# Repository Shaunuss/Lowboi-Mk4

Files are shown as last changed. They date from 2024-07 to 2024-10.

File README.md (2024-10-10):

# **Lowboi Mk4 15:1**

## Badass lightweight worm drive extruder.

Lowboi Mk4 - 003

## PARTS DESCRIPTION  
The drivetrain on Lowboi Mk4 uses a single piece gear hob and bearing idler configuration, resulting in a very smooth and high extrusion quality, practically eliminating the common woodgrain artifacting seen in numerous other extruders. This is down to the gear hob being one piece and fully concentric, and no gear meshing issues sometimes seen in dual drive gear extruders. *Bill of materials is at the bottom.*

*NOTE:* The body/housing of Lowboi Mk4 has been updated with internal reinforcing to strengthen the housing against cracking along layer lines. Following print, you need to superglue two 20mm long pieces of filament up inside two holes from underneath. See video in build tips for more details.

*Optional printed toolboard motor mount bracket is available in the files list.* (requires M3 x 30 capscrews for mounting through motor)

## GEAR  
**K1 steel drive gear hob with DLC coating** is sourced from **AliExpress**, originally intended as an upgrade part for the Creality K1 extruder. I used gears from Mellow and am very happy with the quality. Gear and bearing quality may vary depending on vendor, so I recommend the use of high quality **NSK bearings** including replacing the stock bearing that comes with the gear.


## WORM  
Worm is a high quality steel worm from **KHK** which can come in one or two start configuration, ***cut down to 12mm long***. You are looking at the two start version of the Lowboi Mk4 with a **15:1 drive ratio**. I have also made an extruder body for the one start version for 30:1 drive ratio.


## GREASE  
It is recommended to use grease containing **molybdenum disulphide** for lubricating the worm and gear, for it's increased anti wear properties.


## IDLER BEARING  
Idler is a small bearing mounted in the latch on a **GCR15 bearing steel shaft**. It is technically a fixed unfixed idler without spring, with only a tiny amount of flex in the tensioning latch itself. This provides very strong grip on the filament by the hob.


## MOTOR  
Lowboi Mk4 uses a **NEMA14 36mm** pancake motor with 5mm D shaft configuration.

The **LDO-36STH20-1004AH-RevA-1** motor has 0.1Nm of torque, and can be sourced from Mellow on Aliexpress as a replacement motor for their Cannon extruder. This motor will work, but it becomes a bottleneck and will skip before you run out of grip on the hob.

For a significant torque increase, the BOM specifies a MOONs **CSE14HRA2L4100** motor which has 0.19Nm of torque for considerably more extrusion force, and can be sourced from Formbot's website. You will never run out of torque with this motor.
Motors

## FLOW TESTS
I carry out open air extrusions tests to see flow capability. I tend to use grey or black ASA at 260°C because this filament is a mainstay of my prints. The following tests were all conducted using the same spool of filament, at 260°, unless stated otherwise. 

With the LDO motor, Lowboi Mk4 has been tested to flow up to **31mm^3/s** through a Trianglelab Dragon Ace hotend with the stock 0.4mm nozzle.

With the MOONs motor, the Dragon Ace hotend was able to flow **~35mm^3/s** max on the stock 0.4mm nozzle.

With the addition of the CHT Melt Zone Extender, max flow increased to **45.7mm^3/s**.

Swapping to a 0.5 Bozzle Nozzle increased max flow to **60.1mm^3/s**.

Increasing hotend temp to 300°C increase max flow to **70mm^3/s**.

# 60.1mm^3/s run
https://github.com/user-attachments/assets/7bbf58c4-ef9b-4407-a020-078142051459

# Slow-motion printing vid showing worm drive in action.
https://github.com/user-attachments/assets/c63346ed-cf1d-420c-8268-6457a2b93abd

## BUILD TIPS  
I have printed this in **Polycarbonate**, and **ASA**. Both have worked well.

Print orientation is standing in the normal upright position, on the foot flange, 0.2 layer height with 100% infill, and using automatic supports.

After printing and removing supports, run a 2mm drill bit down through the filament tunnel all the way through the extruder to clear any burrs and prep the tunnel.

Carefully wind a 4mm drill bit by hand through the drive shaft bores, taking care to keep the bit aligned with the holes to avoid removing excess material.

Do the same with a 3mm drill bit through the pivot point bore on the latch. You shouldn't need to do it for the bearing bores unless the shaft is a stubborn fit.

Assemble as per the exploded view, you may need to use polygrip pliers to fit the 4mm driveshaft through the body and bearings.

*Don't forget to cut the worm down to 12mm*.

https://github.com/user-attachments/assets/5c13dc8a-371c-41f1-bb70-907f3756fbca

## CONFIG SETTINGS  

Try these settings to start off with - you may need to tweak rotation distance but this is a great starting point.
```
gear_ratio: 15:1

rotation_distance: 42.3
```

## *Please enjoy Lowboi Mk4 and I would be grateful for your feedback!*

Lowboi Mk4 - 002

## Exploded view with Bill of Materials:
Exploded

## BOM table, for easy copy paste:

| ITEM NO. | PART NUMBER | DESCRIPTION | QTY. | LINK |
|---|---|---|---|---|
| 1 | Body | LOWBOI MK4 BODY - 2 START | 1 | |
| 2 | MR84-ZZ | 4 X 8 X 3 DEEP GROOVE BALL BEARING | 1 | [Link](https://www.aliexpress.com/item/1005006362413271.html) |
| 3 | Bearing Spacer | 8 X 6 X 2.5 BEARING SPACER (PRINTED) | 1 | |
| 4 | K1 Hob Gear | K1 steel hob GEAR - DLC COATED | 1 | [Link](https://www.aliexpress.com/item/1005007288378552.html) |
| 5 | 684-ZZ | 4 X 9 X 4 DEEP GROOVE BALL BEARING | 1 | [Link](https://www.aliexpress.com/item/1005006360598641.html) |
| 6 | 4MM GCR15 | DRIVE SHAFT - Ø4MM X 20MM GCR15 BEARING STEEL PIN | 1 | [Link](https://www.aliexpress.com/item/1005005710466043.html) |
| 7 | CSE14HRA2L4100 | MOONS Ø36 X 20.2 NEMA14 PANCAKE STEPPER | 1 | [Link](https://www.vivedino.com/products/moons-motor-for-marathon?VariantsId=11086) |
| 8 | KHK SW0.5-R2 | KHK 0.5 MODULE TWO START WORM | 1 | [Link](https://www.khkgears.us/catalog/product/SW0.5-R2/) |
| 9 | M3 | M3 FLAT WASHER | 3 | [Link](https://www.aliexpress.com/item/1005002301164770.html) |
| 10 | M03 X 12 | M3 X 12MM CAPSCREW | 2 | [Link](https://www.aliexpress.com/item/1005006342222924.html) |
| 11 | M3 4 x 3 Brass Melt Insert | BRASS MELT INSERT M3 - Ø4MM x 3MM | 1 | |
| 12 | Latch | LOWBOI MK4 IDLER TENSION LATCH | 1 | |
| 13 | Pivot Shaft | PIVOT SHAFT Ø3MM x 20MM GCR15 BEARING STEEL PIN | 1 | [Link](https://www.aliexpress.com/item/1005005710466043.html) |
| 14 | MR83-ZZ | 3 X 8 X 3 DEEP GROOVE BALL BEARING | 1 | [Link](https://www.aliexpress.com/item/1005006378619101.html) |
| 15 | Idler Shaft | IDLER SHAFT - Ø3MM x 10MM GCR15 BEARING STEEL PIN | 1 | [Link](https://www.aliexpress.com/item/1005005710466043.html) |
| 16 | M03 X 10 | M3 X 10MM BUTTON HEAD SCREW | 1 | |
| 17 | Collar | REVERSE BOWDEN RETAINING COLLAR | 1 | |
| 18 | COLLAR Clip | CLIP FOR RETAINING COLLAR | 1 | |

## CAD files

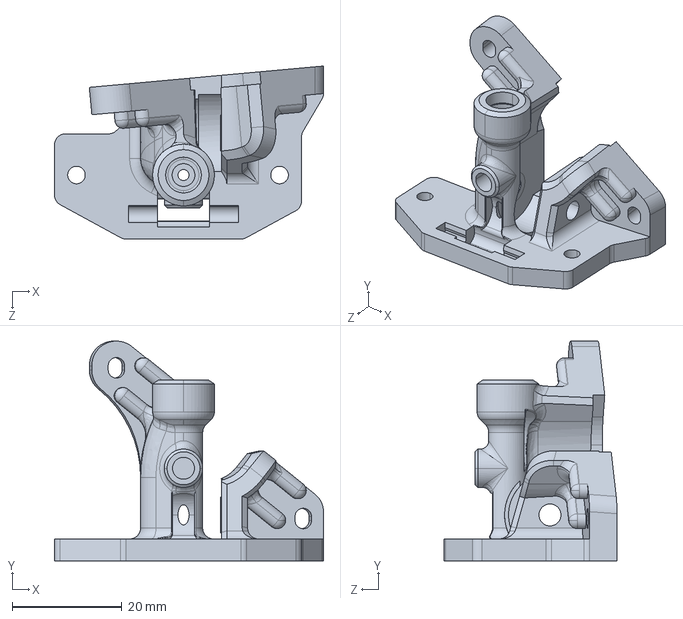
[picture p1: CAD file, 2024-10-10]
Lowboi Mk4 Body - Orbiter 2.0 Mounting - 2 start KHK.STEP
49.0 x 40.0 x 31.5 mm

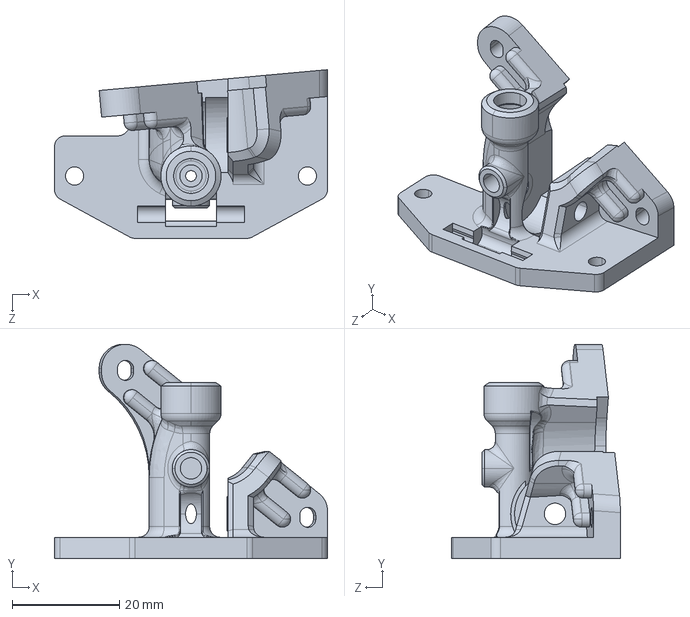
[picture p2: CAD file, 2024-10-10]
Lowboi Mk4 Body - Sherpa Mini Mounting - 2 start KHK.STEP
51.0 x 40.0 x 31.5 mm

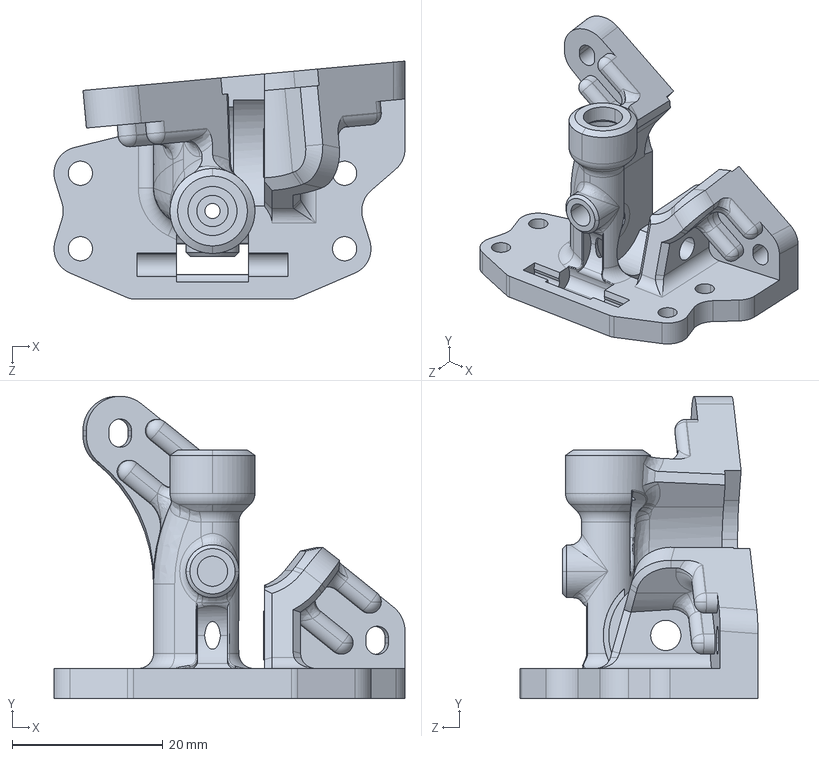
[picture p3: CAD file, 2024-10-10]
Lowboi Mk4 Body - Shaunuss Mounting - 2 start KHK.STEP
46.5 x 40.0 x 31.5 mm

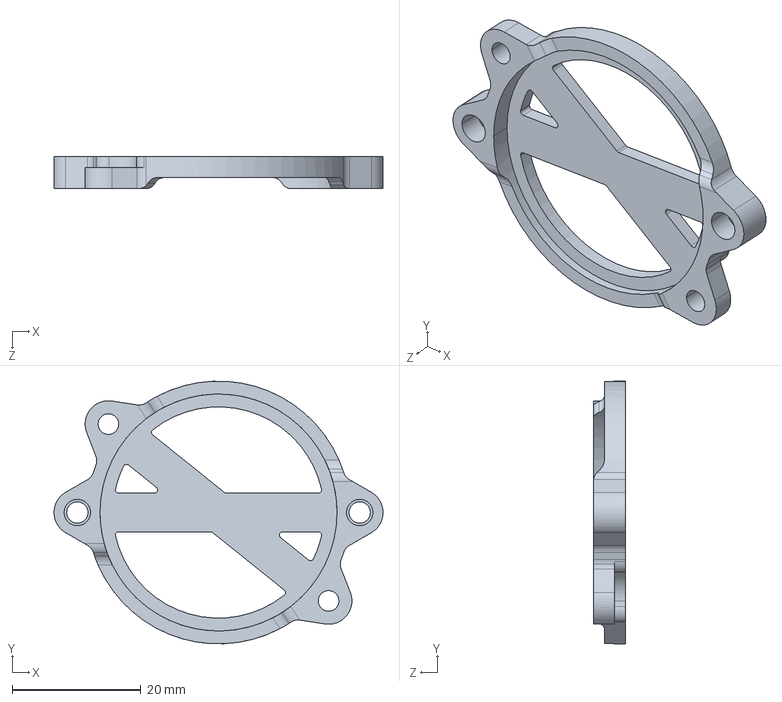
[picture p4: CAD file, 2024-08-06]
Toolboard Motor Mount.STEP
51.1 x 40.8 x 5.00 mm

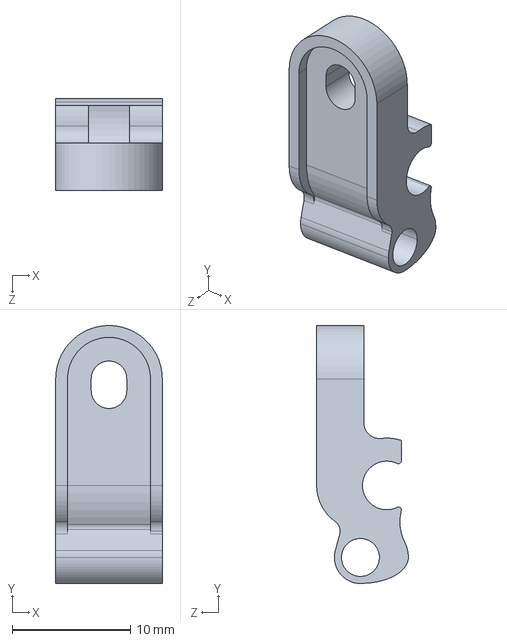
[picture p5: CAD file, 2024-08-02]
Lowboi Mk4 Latch - 4mm idler shaft.STEP
9.00 x 21.8 x 7.75 mm

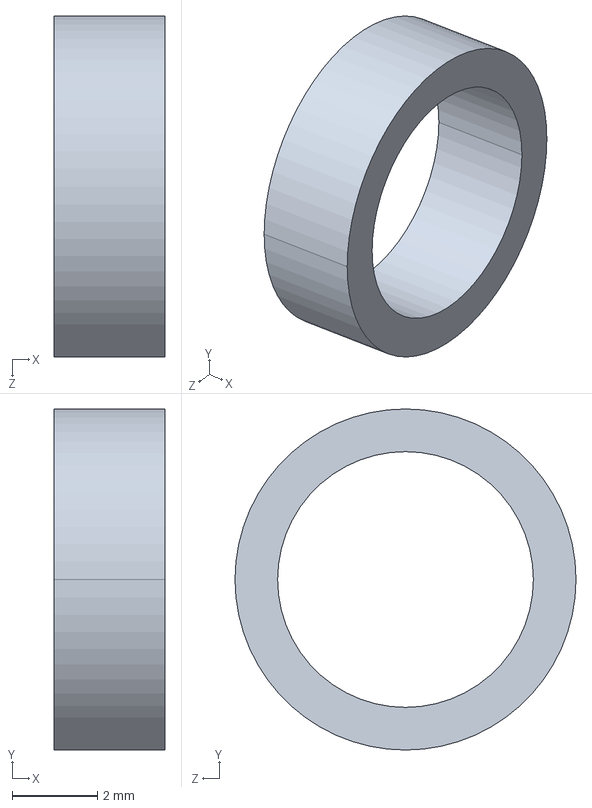
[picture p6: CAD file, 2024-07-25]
Lowboi Mk4 Bearing Spacer.STEP
2.60 x 8.00 x 8.00 mm

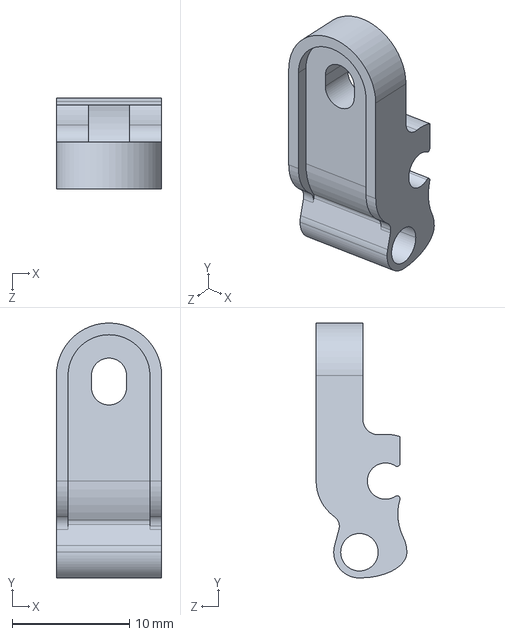
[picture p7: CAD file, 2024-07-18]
Lowboi Mk4 Latch.STEP
9.00 x 21.8 x 7.75 mm

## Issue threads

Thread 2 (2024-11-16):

Sourcing hints / design question

hafriedlander, 2024-11-16:
Hi,

Sorry for raising a mostly-not-an-issue issue. You asked for feedback but I couldn't see another way to reach out.

Sharing my experience around sourcing:

Sourcing the worm was fairly tricky here in New Zealand. The option I chose was to order from Yahoo Japan through a shopping agent (I used https://store.shopping.yahoo.co.jp/kouguland/ts-8566560.html through Goody Japan and was very happy with the service from both, but there are other sources). Alternatively, Double Folded Ascender kits (like https://dfh.fm/products/double-folded-ascender-extruder-kit) would normally contain them too, although that's an expensive way to get them.

I also wasn't sure how to order the Moons motor through Formbot, since they don't list the part numbers. I took a guess at it being the Nema14 at https://www.formbot3d.com/products/moons-motor-for-marathon?VariantsId=11086 and it was, but I'm not sure how much stock they'll have (given it's listed as a spare part, not just a stocked motor). I couldn't find any other source, so this might become an "LDO is your only option" soon.

Question on design:

The other place I've seen worms used on 3D printers is the Z Drive on the Annex Engineering Redoubt (they do love their worms). There they use a thrust bearing to isolate axial loads between the worm and the motor. You probably can't fit one on the filament end (and there isn't enough shaft anyway), but you definitely can fit one on the motor end by extending the backing plate a little. Did you consider using thrust bearings? Have you seen any wear in the stepper bearings from axial loads?

Shaunuss, 2024-11-18:
Hi Hamish, good to hear from a fellow Kiwi. Thanks for taking the time to engage and post up some feedback, it's appreciated!

I used Zenmarket to source the KHK worm, which is another shopping agent for Japan. They were a little slow but worked quite well, and they were cheap. I had friends overseas recommended me Zenmarket, and they have used it themselves to get worms sent to the USA. So it's a decent service.

I should update the git to specify this, but you guessed right in that it is the Nema 14 option from Formbot. I think they will continue to have a decent amount of stock for a while because this motor is the one they use to move their IDEX toolheads in X the axis on their new Marathon printer. But yeah you're not wrong, finding decent grunty pancake motors has been quite a challenge and if Formbot ever stopped stocking them, we'd be back to the LDO.

Regarding the use of thrust washers... previously I have made use of thrust washers on Lowboi Mk2 which used the cannon extruder gears that had angled teeth, and thus imparted a certain amount of side loading on the gears. Here I used thrust washers to constrain the gear centrally on this design.

But I have never used them for mitigating axial loads by putting them on the shaft of the motor between worm and front bearing. I can see the reasoning in wanting to use a thrust washer how you've described, but have never bothered doing so. I can't say I have seen any wear in the stepper bearings but I haven't run the extruder long or hard enough for potential wear to have developed.

You will note the MOONs motor doesn't have a housing enclosing the front bearing, but that the bare bearing itself is protruding from the housing. Due to this, a good way to do it would be using a F5-10M thrust washer stacked against a large washer resting against the outer race of the bearing, with a small counterbore to clear the inner race. Without the large washer, the thrust washer would ineffectually spin with the shaft and the motor bearings would still take the loading. If anyone wants a design revision to accommodate this arrangement, let me know and I will produce the files to suit.

For me I'm just going to keep using it as is because I reckon she'll be right! 😎 I'm never really operating the extruder so hard as to be placing any significant loading along the shaft... so I'll run mine without thrust washer for the foreseeable future. But for anyone who is operating near max extrusion capability, they may be interested in doing so.

hafriedlander, 2024-11-19:
Ah, I hadn't noticed that, and yeah you're right. I was originally test-fitting with an LDO which has a cover, so I was just running one of the F5-10M races pressed against the motor, and the balls directly pressed against the worm (leaving out the other race) for thinness. But that won't work with the Moons.

The Moons spec doesn't have max axial load specified, but a lazy Perplexity query (https://www.perplexity.ai/search/a-1-15-ratio-worm-gear-set-mea-DQhikMmISTuJD8jD.911Qg) gave an estimated axial load on the motor at 2-9N, and https://www.jkongmotor.com/Product/JKM-1-8Deg-Nema-14-Stepper-Motor.html says 10N max axial, so we're in "probably fine" range.

Suich8, 2025-03-26:
Having some trouble sourcing a k1 gear to match bearings. Have tried both a mellow and random amazon one. Bore is 8mm full way, so 684zz is no good. 2 MR84s in theory would work, but both gears I've tried have internal bearing stops that don't allow a flush fit (on mellow, this was on the filament end; on generic, this was on worm end). Already broke a few bits trying to remove stops and am not ready to buy a bit for hardened steel that costs 3x the cost of the gears themselves haha. Any ideas for finding a gear that works?

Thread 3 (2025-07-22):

Stopping extrusione

Oasis1981, 2025-07-22:
Hi...
this seems not occasionally...
it works well for some days, after that it stop extruding without reason....

the r2 round... the wheel round... the motor round... the extruder corpse works... but the filament seems not caputured correctly.
if i push it manually it starts to extrude again... but only for little time..

is it only my issue?

Oasis1981, 2025-07-23:
oh ok, i'm not the only one one :D
so it's a grip problem.
i had the same problem with r1 worm but i thought that it was by my bad design... but i see it's general problem.

interestig the 2 knob.
is there a step  about this new version available? otherwise i'll try to design it by myself.
i have adapted it to my toolhead wip

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

Oasis1981, 2025-07-31:
i've tried this solution but, to me, it's not good.

i can't find the right point, of the equlibrium, between the extrusion and the motor grip (it means that the worm round but the gear didn't move cause there is a opposite force)
caused seems the hotend it's not enought to extrude at 24 mm3. i've tried rapido uhf and dragon ace with mze
little tight the motor grip, little untight there is no extrusion.

but with mk4, i could run over 30 mm3... so the problem is the gears, not the hotend

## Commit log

2024-07-25 Update README.md
    Added remix housing
2024-08-02 added a latch with a 4mm idler shaft option
    This lets people use MR84ZZ bearing in the latch. But you'll need to file the filament tunnel a bit to make clearance for the larger shaft
    [Lowboi Mk4 Latch - 4mm idler shaft.STEP]
2024-08-06 Add files via upload
    added toolboard motor mount bracket
    [Toolboard Motor Mount.STEP]
